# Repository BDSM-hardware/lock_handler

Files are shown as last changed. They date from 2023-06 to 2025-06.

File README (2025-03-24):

This module handles a collective bondage and/or multiple points self bondage.
It checks all the locks are closed and locks. If the lock is lost for one, all the locks unlock.

For the details, see the INSTALL file.

It has many LED to follow the procedure and see where is the problem, if so.
For each channel, a green and an amber LED tells if it is detected or not.
If all the detections of all the modules are on, the LEDs switch off and an amber LED per module illuminates.
When it is locked the amber switches off and a set of 2 red LED illuminates.
If a module is unused a switch turns everything off, tells to the daisy-chain it is OK, discards the lock command and illuminates a blue LED.

It is designed as small modules of 4 detection inputs. There is a daisy-chain in between.
* Mode 1: The system waits everybody is ready to lock, and illuminate an all ready LED. By connecting two wires to each other, it locks. By opening or shorting to the ground, it unlocks.
* Mode 2: It is similar to mode 1 but it locks as soon as everybody is ready without external action (remote control, timer etc...). This spares some wires.

Each input channel has a soft and a hard input. There is a dilemma between:
* a too strong detection that can detect the bondage is open, and unlock everybody.
* a too soft detection that can make a lock opening later.
To fix that, the hard and the soft are needed to lock. Only the soft is needed to maintain.
If a switch style detection is used, that can be done with 2 switches. If a metal detector style detection is used, it is two thresholds.
If this feature is not used, the two can be connected together.

It is a component.
* The output is a transistor. The user can add the power circuits needed against the lock chosen (electro magnet, pneumatic output etc...).
* The board is designed to run in stand alone mode with switches directly cconnected or with an additional board. It is mostly a metal detector style circuit. However, some components differs.

There is no circuit to program, no PIC, noFPGA, noCPLD etc... It works as soon as the 74HCxx and other components are soldered. It uses through hole components, not SMD.

Some VHDL files are provided to describe the behaviour in a more human-readable way.
A test is provided to check the truth table is the same for both the behaviour file and the file exported from the schematic.

TODO
* Add instructions using the bottom silk
* Build a prototype

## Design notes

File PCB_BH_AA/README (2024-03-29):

To get the files of the 2 inputs versions, switch to the lock_handler_2 branch.

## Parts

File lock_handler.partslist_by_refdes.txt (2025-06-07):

.START
..refdes	device	value	tolerance	comment	footprint	quantity
C1	CAPACITOR	4.7uF	20%	/	100mil	1
C11	POLARIZED_CAPACITOR	4.7uF	20%	Neg supply only	unknown	1
C12	POLARIZED_CAPACITOR	4.7uF	20%	Neg supply only	unknown	1
C13	POLARIZED_CAPACITOR	4.7uF	20%	Neg supply only	unknown	1
C14	POLARIZED_CAPACITOR	4.7uF	20%	Neg supply only	unknown	1
C15	CAPACITOR	2.2uF	20%	MLCC	2.54	1
C16	CAPACITOR	2.2uF	20%	MLCC	2.54	1
C17	CAPACITOR	2.2uF	20%	MLCC	2.54	1
C18	CAPACITOR	2.2uF	20%	MLCC	2.54	1
C19	CAPACITOR	2.2uF	20%	MLCC	2.54	1
C2	CAPACITOR	4.7uF	20%	/	100mil	1
C20	CAPACITOR	2.2uF	20%	MLCC	2.54	1
C21	CAPACITOR	2.2uF	20%	MLCC	2.54	1
C22	CAPACITOR	2.2uF	20%	MLCC	2.54	1
C23	POLARIZED_CAPACITOR	22uF	20%	tantale 50V	1000mil	1
C24	POLARIZED_CAPACITOR	220uF	40%	aluminium 16V	800mil	1
C25	POLARIZED_CAPACITOR	10uF	20%	or more	200mil	1
C26	POLARIZED_CAPACITOR	10uF	20%	or more	200mil	1
C27	CAPACITOR	1uF	20%	or more	100mil	1
C28	CAPACITOR	1uF	20%	or more	100mil	1
C29	CAPACITOR	1uF	20%	or more	100mil	1
C3	CAPACITOR	4.7uF	unknown	unknown	100mil	1
C30	CAPACITOR	1uF	20%	or more	100mil	1
C31	CAPACITOR	2.2uF	20%	MLCC	2.54	1
C4	CAPACITOR	4.7uF	unknown	unknown	100mil	1
C5	CAPACITOR	4.7uF	unknown	unknown	100mil	1
C6	CAPACITOR	4.7uF	20%	/	100mil	1
CONN_ABCD_DATA	CONNECTOR_7	/	/	/	SIP7N	1
CONN_ABCD_POWER	CONNECTOR_7	unknown	unknown	unknown	SIP7N	1
CONN_CHAIN	CONNECTOR_6	/	/	/	SIP6N	1
CONN_CHAIN_NEXT	CONNECTOR_6	/	/	/	SIP6N	1
CONN_DISABLE	CONNECTOR_2	/	/	/	SIP2N	1
CONN_NO_N_S	CONNECTOR_2	unknown	unknown	Neg supply to ground	SIP2N	1
CONN_OUTPUT	CONNECTOR_3	/	/	/	SIP3N	1
CONN_POWER	CONNECTOR_8	/	/	/	SIP8N	1
CONN_POWER_NEXT	CONNECTOR_8	/	/	/	SIP8N	1
CONN_RING	CONNECTOR_2	unknown	/	/	SIP2N	1
D10	DIODE	1N4148	/	Neg supply only	300mil	1
D11	DIODE	BA158	/	/	400mil	1
D12	DIODE	BA158	/	Neg supply only	400mil	1
D13	DIODE	BA158	/	/	400mil	1
D3	DIODE	1N4148	/	Neg supply only	300mil	1
D4	DIODE	1N4148	/	Neg supply only	300mil	1
D5	DIODE	1N4148	/	Neg supply only	300mil	1
D6	DIODE	1N4148	/	Neg supply only	300mil	1
D7	DIODE	1N4148	/	Neg supply only	300mil	1
D8	DIODE	1N4148	/	Neg supply only	300mil	1
D9	DIODE	1N4148	/	Neg supply only	300mil	1
LED1	LED	C503B-BCN	/	bleue	5.08	1
LED10	LED	C503B-ACN	/	amber	5.08	1
LED11	LED	C503B-RCN	/	red	5.08	1
LED12	LED	C503B-RCN	/	red	5.08	1
LED13	LED	C503B-WCN	/	white	5.08	1
LED2	LED	C503B-GCN	/	green	5.08	1
LED3	LED	C503B-ACN	/	amber	5.08	1
LED4	LED	C503B-GCN	/	green	5.08	1
LED5	LED	C503B-ACN	/	amber	5.08	1
LED6	LED	C503B-GCN	/	green	5.08	1
LED7	LED	C503B-ACN	/	amber	5.08	1
LED8	LED	C503B-GCN	/	green	5.08	1
LED9	LED	C503B-ACN	/	amber	5.08	1
Q1	NPN_TRANSISTOR	2N3904	Or equiv. CBE	/	TO92	1
Q2	NPN_TRANSISTOR	2N3904	Or equiv. CBE	/	TO92	1
Q3	darlington, NPN	TIP120	/	Or equiv. BCE darlington Vce twice the lock voltage	TO92	1
R14	RESISTOR	1.15K	10%, R211 to R217 diff 1%	/	500mil	1
R15	RESISTOR	1.15K	10%, R211 to R217 diff 1%	/	500mil	1
R16	RESISTOR	1.15K	10%, R211 to R217 diff 1%	/	500mil	1
R17	RESISTOR	1.15K	10%, R211 to R217 diff 1%	/	500mil	1
R18	RESISTOR	1.15K	10%, R211 to R217 diff 1%	/	500mil	1
R19	RESISTOR	1.15K	10%, R211 to R217 diff 1%	/	500mil	1
R20	RESISTOR	1.15K	10%, R211 to R217 diff 1%	/	500mil	1
R21	RESISTOR	1.15K	10%, R211 to R217 diff 1%	/	500mil	1
R22	RESISTOR	1.15K	10%, R211 to R217 diff 1%	/	500mil	1
R23	RESISTOR	1.15K	10%, R211 to R217 diff 1%	/	500mil	1
R24	RESISTOR	1.15K	10%, R211 to R217 diff 1%	/	500mil	1
R25	RESISTOR	1.15K	10%, R211 to R217 diff 1%	/	500mil	1
R26	RESISTOR	2.7K	10%	/	500mil	1
R27	RESISTOR	2.7K	10%	/	500mil	1
R28	RESISTOR	47.5	10%	/	500mil	1
R29	RESISTOR	22.1R	10%	/	500mil	1
R30	RESISTOR	4.7K	10%	/	500mil	1
R31	RESISTOR	4.7K	10%	/	500mil	1
R32	RESISTOR	348K	10%	/	500mil	1
R33	RESISTOR	10K	10%	/	500mil	1
R34	RESISTOR	10K	10%	/	500mil	1
R35	RESISTOR	10K	10%	/	500mil	1
R36	RESISTOR	10K	10%	/	500mil	1
R37	RESISTOR	22.1R	10%	/	500mil	1
R38	RESISTOR	22.1R	10%	/	500mil	1
R39	RESISTOR	4.7K	10%	/	500mil	1
R40	RESISTOR	22.1R	10%	/	500mil	1
R41	RESISTOR	10K	10%	/	500mil	1
R42	RESISTOR	22.1R	10%	/	500mil	1
R43	RESISTOR	1K	10%	value half the lock device resistance	500mil	1
R44	RESISTOR	1.15K	10%	/	500mil	1
R45	RESISTOR	221K	10%	/	500mil	1
R46	RESISTOR	4.75K	10%	/	500mil	1
R47	RESISTOR	4.75K	10%	/	500mil	1
R48	RESISTOR	221K	10%	/	500mil	1
R49	RESISTOR	4.75K	10%	/	500mil	1
R50	RESISTOR	4.75K	10%	/	500mil	1
R51	RESISTOR	221K	10%	/	500mil	1
R52	RESISTOR	4.75K	10%	/	500mil	1
R53	RESISTOR	4.75K	10%	/	500mil	1
R54	RESISTOR	221K	10%	/	500mil	1
R55	RESISTOR	4.75K	10%	/	500mil	1
R56	RESISTOR	4.75K	10%	/	500mil	1
R57	RESISTOR	221K	10%	/	500mil	1
R58	RESISTOR	4.75K	10%	/	500mil	1
R59	RESISTOR	4.75K	10%	/	500mil	1
R60	RESISTOR	221K	10%	/	500mil	1
R61	RESISTOR	4.75K	10%	/	500mil	1
R62	RESISTOR	4.75K	10%	/	500mil	1
R63	RESISTOR	221K	10%	/	500mil	1
R64	RESISTOR	4.75K	10%	/	500mil	1
R65	RESISTOR	4.75K	10%	/	500mil	1
R66	RESISTOR	221K	10%	/	500mil	1
R67	RESISTOR	4.75K	10%	/	500mil	1
R68	RESISTOR	4.75K	10%	/	500mil	1
R69	RESISTOR	681R	2%	/	500mil	1
R70	RESISTOR	681R	2%	or zener diode	500mil	1
R71	RESISTOR	681R	2%	or zener diode	500mil	1
R76	RESISTOR	2.21K	2%	Switches only	500mil	1
R77	RESISTOR	2.21K	2%	Switches only	500mil	1
R78	RESISTOR	2.21K	2%	Switches only	500mil	1
R79	RESISTOR	2.21K	2%	Switches only	500mil	1
R80	RESISTOR	4.7K	10%	/	500mil	1
R81	RESISTOR	22.1R	10%	/	500mil	1
RP45	RESISTORPACK_9	10K	10%	Neg supply only	8X100mil	1
U1	7400	74HC00	/	/	DIP14	1
U10	7404	74HC04	/	/	DIP14	1
U11	QUAD_OPAMP	TLV9144IN	/	/	DIL14	1
U12	QUAD_OPAMP	TLV9144IN	/	/	DIL14	1
U13	icl7660	unknown	/	Neg supply only	DIL8	1
U14	7806	7806	/	7805 or 7806	TO220	1
U15	7906	7906	unknown	Neg supply only	TO220	1
U16	7809	unknown	unknown	Neg supply and alim > 10V	TO220	1
U2	7402	74HC02	/	/	DIP14	1
U3	7404	74HC04	/	/	DIP14	1
U4	7420	74HC20	/	/	DIP14	1
U5	7400	74HC00	/	/	DIP14	1
U7	7400	74HC00	/	/	DIP14	1
U8	7400	74HC00	/	/	DIP14	1
U9	74132	74HC132	/	/	DIP14	1
.END

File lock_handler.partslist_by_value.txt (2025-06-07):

.START
..device	value	tolerance	comment	footprint	quantity	refdes
7400	74HC00	/	/	DIP14	4	U1 U5 U7 U8
7402	74HC02	/	/	DIP14	1	U2
7404	74HC04	/	/	DIP14	2	U10 U3
74132	74HC132	/	/	DIP14	1	U9
7420	74HC20	/	/	DIP14	1	U4
7806	7806	/	7805 or 7806	TO220	1	U14
7809	unknown	unknown	Neg supply and alim > 10V	TO220	1	U16
7906	7906	unknown	Neg supply only	TO220	1	U15
CAPACITOR	1uF	20%	or more	100mil	4	C27 C28 C29 C30
CAPACITOR	2.2uF	20%	MLCC	2.54	9	C15 C16 C17 C18 C19 C20 C21 C22 C31
CAPACITOR	4.7uF	20%	/	100mil	3	C1 C2 C6
CAPACITOR	4.7uF	unknown	unknown	100mil	3	C3 C4 C5
CONNECTOR_2	/	/	/	SIP2N	1	CONN_DISABLE
CONNECTOR_2	unknown	/	/	SIP2N	1	CONN_RING
CONNECTOR_2	unknown	unknown	Neg supply to ground	SIP2N	1	CONN_NO_N_S
CONNECTOR_3	/	/	/	SIP3N	1	CONN_OUTPUT
CONNECTOR_6	/	/	/	SIP6N	2	CONN_CHAIN CONN_CHAIN_NEXT
CONNECTOR_7	/	/	/	SIP7N	1	CONN_ABCD_DATA
CONNECTOR_7	unknown	unknown	unknown	SIP7N	1	CONN_ABCD_POWER
CONNECTOR_8	/	/	/	SIP8N	2	CONN_POWER CONN_POWER_NEXT
darlington, NPN	TIP120	/	Or equiv. BCE darlington Vce twice the lock voltage	TO92	1	Q3
DIODE	1N4148	/	Neg supply only	300mil	8	D10 D3 D4 D5 D6 D7 D8 D9
DIODE	BA158	/	/	400mil	2	D11 D13
DIODE	BA158	/	Neg supply only	400mil	1	D12
icl7660	unknown	/	Neg supply only	DIL8	1	U13
LED	C503B-ACN	/	amber	5.08	5	LED10 LED3 LED5 LED7 LED9
LED	C503B-BCN	/	bleue	5.08	1	LED1
LED	C503B-GCN	/	green	5.08	4	LED2 LED4 LED6 LED8
LED	C503B-RCN	/	red	5.08	2	LED11 LED12
LED	C503B-WCN	/	white	5.08	1	LED13
NPN_TRANSISTOR	2N3904	Or equiv. CBE	/	TO92	2	Q1 Q2
POLARIZED_CAPACITOR	10uF	20%	or more	200mil	2	C25 C26
POLARIZED_CAPACITOR	220uF	40%	aluminium 16V	800mil	1	C24
POLARIZED_CAPACITOR	22uF	20%	tantale 50V	1000mil	1	C23
POLARIZED_CAPACITOR	4.7uF	20%	Neg supply only	unknown	4	C11 C12 C13 C14
QUAD_OPAMP	TLV9144IN	/	/	DIL14	2	U11 U12
RESISTOR	1.15K	10%	/	500mil	1	R44
RESISTOR	1.15K	10%, R211 to R217 diff 1%	/	500mil	12	R14 R15 R16 R17 R18 R19 R20 R21 R22 R23 R24 R25
RESISTOR	10K	10%	/	500mil	5	R33 R34 R35 R36 R41
RESISTOR	1K	10%	value half the lock device resistance	500mil	1	R43
RESISTOR	2.21K	2%	Switches only	500mil	4	R76 R77 R78 R79
RESISTOR	2.7K	10%	/	500mil	2	R26 R27
RESISTOR	22.1R	10%	/	500mil	6	R29 R37 R38 R40 R42 R81
RESISTOR	221K	10%	/	500mil	8	R45 R48 R51 R54 R57 R60 R63 R66
RESISTOR	348K	10%	/	500mil	1	R32
RESISTOR	4.75K	10%	/	500mil	16	R46 R47 R49 R50 R52 R53 R55 R56 R58 R59 R61 R62 R64 R65 R67 R68
RESISTOR	4.7K	10%	/	500mil	4	R30 R31 R39 R80
RESISTOR	47.5	10%	/	500mil	1	R28
RESISTOR	681R	2%	/	500mil	1	R69
RESISTOR	681R	2%	or zener diode	500mil	2	R70 R71
RESISTORPACK_9	10K	10%	Neg supply only	8X100mil	1	RP45
.END

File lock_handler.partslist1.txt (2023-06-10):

.START
..refdes	device	value	tolerance	comment	footprint	quantity
C200	CAPACITOR	2.2uF	20%	/	2.54	1
C201	CAPACITOR	2.2uF	20%	/	2.54	1
C202	CAPACITOR	2.2uF	20%	/	2.54	1
C203	CAPACITOR	2.2uF	20%	MLCC	2.54	1
C204	CAPACITOR	2.2uF	20%	MLCC	2.54	1
C205	CAPACITOR	2.2uF	20%	MLCC	2.54	1
C206	CAPACITOR	2.2uF	20%	MLCC	2.54	1
C207	CAPACITOR	2.2uF	20%	MLCC	2.54	1
C208	CAPACITOR	2.2uF	20%	MLCC	2.54	1
C209	CAPACITOR	2.2uF or 1nF	10%	/	2.54	1
C210	CAPACITOR	2.2uF or 1nF	10%	/	2.54	1
C211	CAPACITOR	2.2uF or 1nF	10%	/	2.54	1
C212	CAPACITOR	2.2uF or 1nF	10%	/	2.54	1
C213	POLARIZED_CAPACITOR	22uF	20%	tantale 50V	5.08	1
C214	POLARIZED_CAPACITOR	220uF	40%	aluminium 16V	2000mil	1
CONN_AB_HARDSOFT	CONNECTOR_7	/	/	/	SIP7N	1
CONN_AB_POWER	CONNECTOR_7	/	/	Elec detec. only	SIP7N	1
CONN_CHAIN	CONNECTOR_6	/	/	/	SIP6N	1
CONN_CHAIN_NEXT	CONNECTOR_6	/	/	/	SIP6N	1
CONN_DISABLE	CONNECTOR_2	/	/	/	SIP2N	1
CONN_OUTPUT	CONNECTOR_3	/	/	/	SIP3N	1
CONN_POWER	CONNECTOR_8	/	/	/	SIP8N	1
CONN_POWER_NEXT	CONNECTOR_8	/	/	/	SIP8N	1
CONN_RING	CONNECTOR_2	/	/	/	SIP2N	1
D200	DIODE	BA158	/	/	300mil	1
D201	DIODE	1N4148	/	Elec detec. only	300mil	1
D202	DIODE	1N4148	/	Elec detec. only	300mil	1
D203	DIODE	1N4148	/	Elec detec. only	300mil	1
D204	DIODE	1N4148	/	Elec detec. only	300mil	1
D205	DIODE	BA158	/	/	300mil	1
LED1	LED	C503B-BCN	/	bleue	5.08	1
LED2	LED	C503B-GCN	/	green	5.08	1
LED3	LED	C503B-ACN	/	amber	5.08	1
LED4	LED	C503B-GCN	/	green	5.08	1
LED5	LED	C503B-ACN	/	amber	5.08	1
LED6	LED	C503B-ACN	/	amber	5.08	1
LED7	LED	C503B-RCN	/	red	5.08	1
LED8	LED	C503B-RCN	/	red	5.08	1
Q200	NPN_TRANSISTOR	2N3904	Or equiv. CBE	/	TO92	1
Q201	darlington, NPN	TIP120	/	Or equiv. BCE darlington Vce twice the lock voltage	TO92	1
Q202	7806	7806	/	7805 or 7806	TO220	1
R200	RESISTOR	4.7K	10%	/	500mil	1
R201	RESISTOR	348K	10%	/	500mil	1
R202	RESISTOR	4.7K	10%	/	500mil	1
R203	RESISTOR	47.5	10%	/	500mil	1
R204	RESISTOR	10K	10%	/	500mil	1
R205	RESISTOR	10K	10%	/	500mil	1
R206	RESISTOR	22.1	10%	/	500mil	1
R207	RESISTOR	22.1	10%	/	500mil	1
R208	RESISTOR	22.1	10%	/	500mil	1
R209	RESISTOR	22.1	10%	/	500mil	1
R210	RESISTOR	10K	10%	/	500mil	1
R211	RESISTOR	1.15K	10%, R211 to R217 diff 1%	/	500mil	1
R212	RESISTOR	1.15K	10%, R211 to R217 diff 1%	/	500mil	1
R213	RESISTOR	1.15K	10%, R211 to R217 diff 1%	/	500mil	1
R214	RESISTOR	1.15K	10%, R211 to R217 diff 1%	/	500mil	1
R215	RESISTOR	1.15K	10%, R211 to R217 diff 1%	/	500mil	1
R216	RESISTOR	1.15K	10%, R211 to R217 diff 1%	/	500mil	1
R217	RESISTOR	1.15K	10%, R211 to R217 diff 1%	/	500mil	1
R218	RESISTOR	1.15K	10%	/	500mil	1
R219	RESISTOR	1K	10%	value half the lock device resistance	500mil	1
R220	RESISTOR	22.1	10%	Switch detec. only	500mil	1
R221	RESISTOR	22.1	10%	Switch detec. only	500mil	1
R222	RESISTOR	22.1	10%	Switch detec. only	500mil	1
R223	RESISTOR	22.1	10%	Switch detec. only	500mil	1
R224	RESISTOR	22.1	10%	/	500mil	1
R225	RESISTOR	22.1	10%	/	500mil	1
R226	RESISTOR	22.1	10%	/	500mil	1
R227	RESISTOR	22.1	10%	/	500mil	1
R228	RESISTORPACK_5	4.7K	10%, diff. 10%	Elec detec. only	2.54	1
R229	RESISTORPACK_5	4.7K	10%, diff. 10%	NC Switch detec. only	2.54	1
R230	RESISTORPACK_5	10K	10%, diff. 10%	NO Switch detec. only	2.54	1
R231	RESISTOR	22.1	10%	NO Switch detec. only	500mil	1
R232	RESISTOR	22.1	10%	NO Switch detec. only	500mil	1
R233	RESISTOR	10K	10%	/	500mil	1
U200	74132	74HC132	/	/	DIP14	1
U201	7404	74HC04	/	/	DIP14	1
U202	7402	74HC02	/	/	DIP14	1
U203	7402	74HC02	/	/	DIP14	1
U204	7410	74HC10	/	/	DIP14	1
U205	7404	74HC04	/	/	DIP14	1
.END

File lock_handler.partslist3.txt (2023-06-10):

.START
..device	value	tolerance	comment	footprint	quantity	refdes
7402	74HC02	/	/	DIP14	2	U202 U203
7404	74HC04	/	/	DIP14	2	U201 U205
7410	74HC10	/	/	DIP14	1	U204
74132	74HC132	/	/	DIP14	1	U200
7806	7806	/	7805 or 7806	TO220	1	Q202
CAPACITOR	2.2uF	20%	/	2.54	3	C200 C201 C202
CAPACITOR	2.2uF	20%	MLCC	2.54	6	C203 C204 C205 C206 C207 C208
CAPACITOR	2.2uF or 1nF	10%	/	2.54	4	C209 C210 C211 C212
CONNECTOR_2	/	/	/	SIP2N	2	CONN_DISABLE CONN_RING
CONNECTOR_3	/	/	/	SIP3N	1	CONN_OUTPUT
CONNECTOR_6	/	/	/	SIP6N	2	CONN_CHAIN CONN_CHAIN_NEXT
CONNECTOR_7	/	/	/	SIP7N	1	CONN_AB_HARDSOFT
CONNECTOR_7	/	/	Elec detec. only	SIP7N	1	CONN_AB_POWER
CONNECTOR_8	/	/	/	SIP8N	2	CONN_POWER CONN_POWER_NEXT
darlington, NPN	TIP120	/	Or equiv. BCE darlington Vce twice the lock voltage	TO92	1	Q201
DIODE	1N4148	/	Elec detec. only	300mil	4	D201 D202 D203 D204
DIODE	BA158	/	/	300mil	2	D200 D205
LED	C503B-ACN	/	amber	5.08	3	LED3 LED5 LED6
LED	C503B-BCN	/	bleue	5.08	1	LED1
LED	C503B-GCN	/	green	5.08	2	LED2 LED4
LED	C503B-RCN	/	red	5.08	2	LED7 LED8
NPN_TRANSISTOR	2N3904	Or equiv. CBE	/	TO92	1	Q200
POLARIZED_CAPACITOR	220uF	40%	aluminium 16V	2000mil	1	C214
POLARIZED_CAPACITOR	22uF	20%	tantale 50V	5.08	1	C213
RESISTOR	1.15K	10%	/	500mil	1	R218
RESISTOR	1.15K	10%, R211 to R217 diff 1%	/	500mil	7	R211 R212 R213 R214 R215 R216 R217
RESISTOR	10K	10%	/	500mil	4	R204 R205 R210 R233
RESISTOR	1K	10%	value half the lock device resistance	500mil	1	R219
RESISTOR	22.1	10%	/	500mil	12	R206 R207 R208 R209 R220 R221 R222 R223 R224 R225 R226 R227
RESISTOR	22.1	10%	NO Switch detec. only	500mil	2	R231 R232
RESISTOR	348K	10%	/	500mil	1	R201
RESISTOR	4.7K	10%	/	500mil	2	R200 R202
RESISTOR	47.5	10%	/	500mil	1	R203
RESISTORPACK_5	10K	10%, diff. 10%	NO Switch detec. only	2.54	1	R230
RESISTORPACK_5	4.7K	10%, diff. 10%	Elec detec. only	2.54	1	R228
RESISTORPACK_5	4.7K	10%, diff. 10%	NC Switch detec. only	2.54	1	R229
.END

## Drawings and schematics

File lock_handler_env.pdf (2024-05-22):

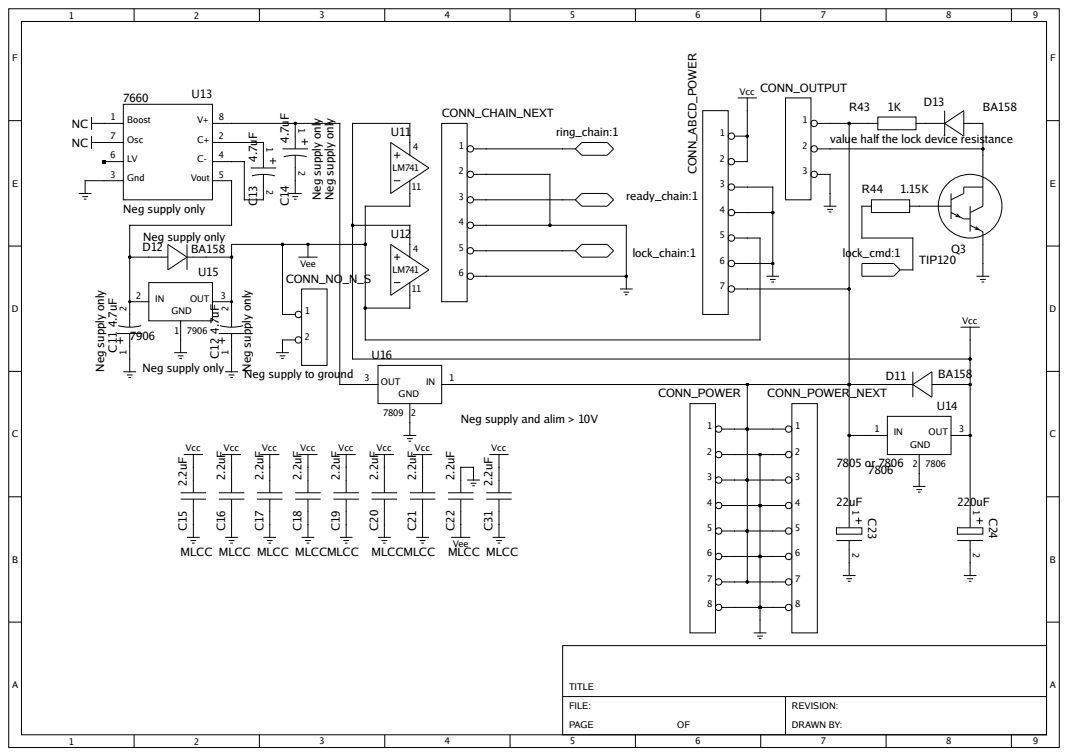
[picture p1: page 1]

value half the lock device resistance

Neg supply to ground

Neg supply and alim > 10V

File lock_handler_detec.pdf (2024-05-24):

TL064 56

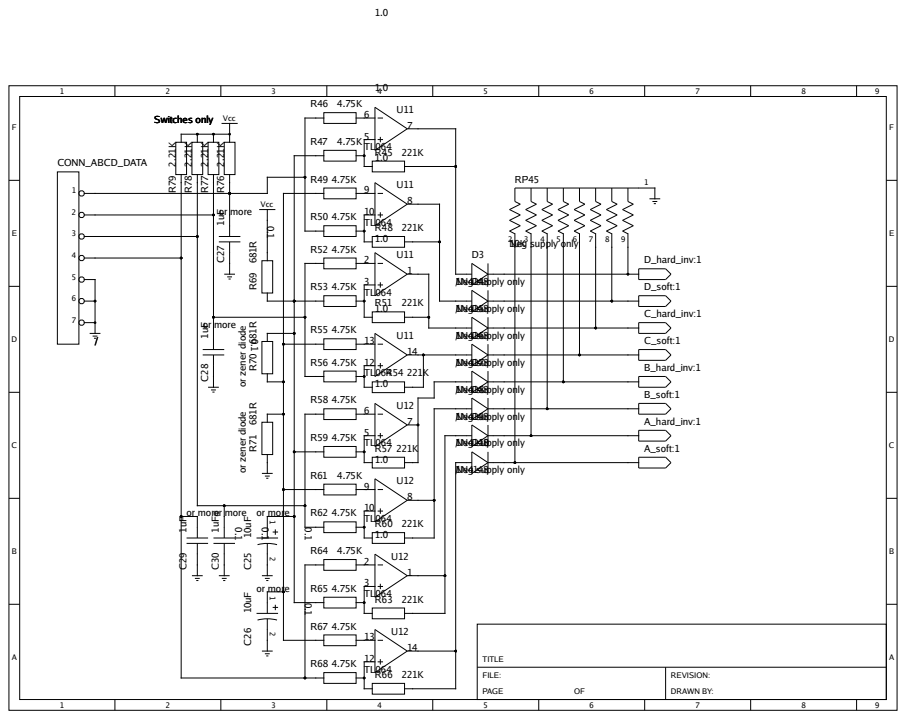
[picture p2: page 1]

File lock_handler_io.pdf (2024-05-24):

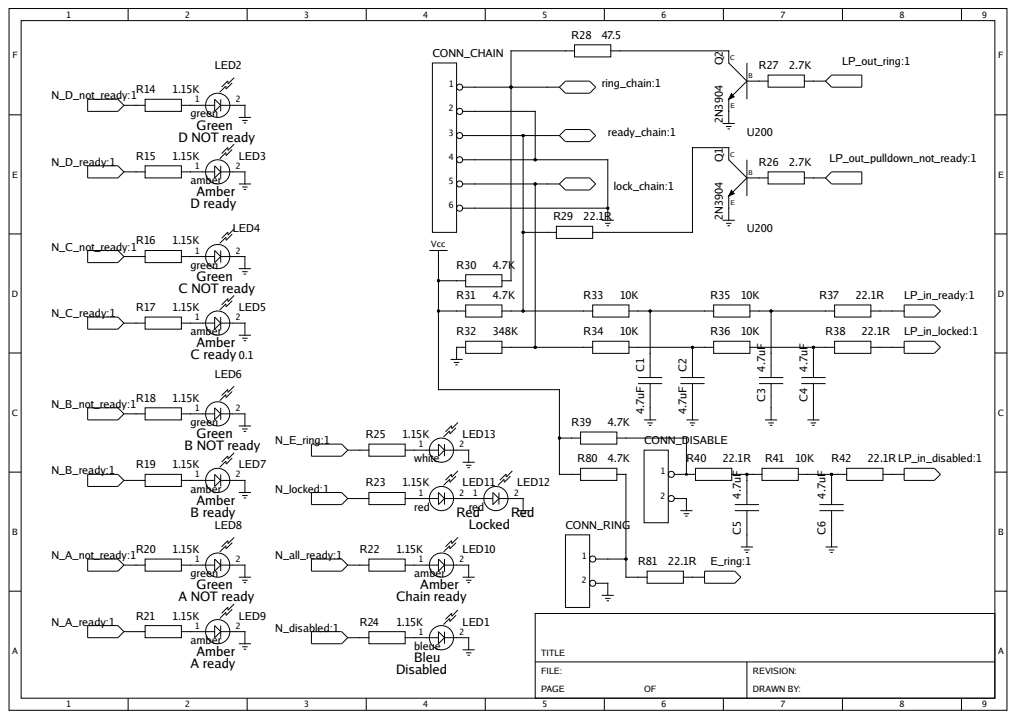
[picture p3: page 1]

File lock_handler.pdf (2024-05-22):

74HC04 1

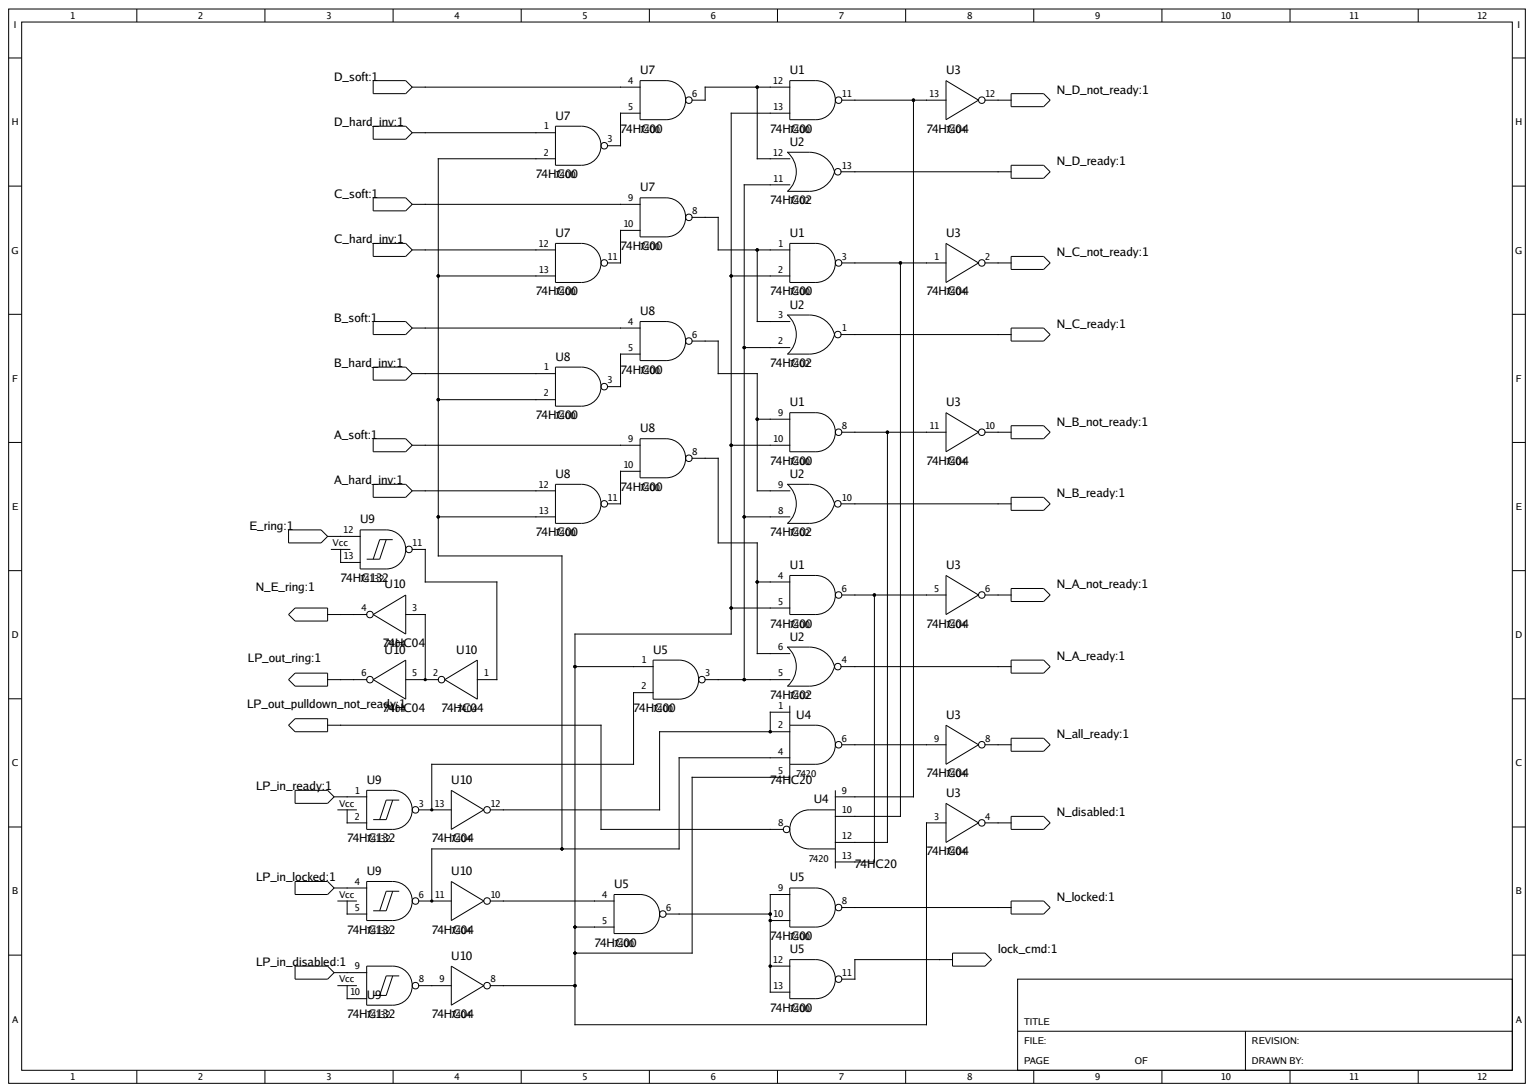
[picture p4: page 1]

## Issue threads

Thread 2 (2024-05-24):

Ring button input forgotten

BDSM-hardware, 2024-05-24:
In the 4 locks version, the ring button has been integrated into the design.
Unfortunately their inputs has been forgotten.

BDSM-hardware, 2024-05-24:
Work around if one does not use the ring button:
strap the pins 12 and 13 of U9 together.
Work around if one uses the ring button and has already made the PCB:
add R80 and R81 with some silicone and wires. It is not that difficult, see the new versions of the PCB

BDSM-hardware, 2024-05-24:
Fixed

Closed 2024-05-24.

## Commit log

2023-05-09 Initial files
    [lock_handler.sch]
2023-05-14 Improve the naming of the files.
    lock_handler.eps beomes lock_handler.pcb.ps
    more ps files are comming with pcb details or schematics export
2023-05-14 Some improvements
    * More .ps and/or .pdf exports
    * Partlists exports
    * PCB went forward
    [lock_handler.sch]
2023-05-14 More PCB work
    * Add room for the decoupling capacitors
    * Draw power supplies, and add high speed printed decoupling capacitors
    * Add mounting screw and partial outline
    * Add a plane for the LED cut out
2023-05-15 More PCB and fix a PS export problem
2023-05-26 More work
    Add a schematic for the decoupling and the passive components for the standalone mode (simple switches)
    The lock_handler.sch schematic is in RC state.
    PCB: Daisy chain passive components completed.
    PCB: Estimation of the passive components of the switches.
    PCB: complete Vcc and ground planes, including some high frequency printed low value decoupling.
    The top of the PCB is in RC state.
    [lock_handler.sch, lock_handler_env.sch]
2023-05-26 Fix a lock_handler.pcb.ps not recognized on some systems
2023-05-28 More work
    * schematic: completed the input part
    * schematic: added the voltage regulator
    * partslists exports: added the columns toleance and comment
    * pcb: improved
    [lock_handler.sch, lock_handler_env.sch]
2023-06-02 Schematic and PCB work
    All the schematics diagrams are now in RC state
    Dimensions of the PCB are now known
    Four components and 34 rat lines are remaining
    [lock_handler.sch, lock_handler_env.sch]
2023-06-02 Fix a clip problem for the .ps export of the PCB
2023-06-10 All schematic and partslist files in RC state
    Before release
    * PCB file is going to be committed
    * Some verification is needed
    * An export in Gerbert is going to be done
    [lock_handler.sch, lock_handler_env.sch]
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2023-06-11 RC of the project
    RC state of the pcb file
    Initial release of the Gerber exports
    [PCB_BH_AA.bottom.gbr, PCB_BH_AA.bottommask.gbr, PCB_BH_AA.bottompaste.gbr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]
2023-12-17 Mechanical drawings updates
    Precise quotation added.
    Corners for the 1591D box.
    TODO: improve the box drawings.
    [PCB_BH_AA.bottom.gbr, PCB_BH_AA.bottommask.gbr, PCB_BH_AA.bottompaste.gbr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]
2024-01-04 Fix a resistor too high
    [lock_handler.sch]
2024-01-04 Initial version of the 4 channels
    [lock_handler.sch, lock_handler_io.sch]
2024-01-07 Some progress
    * Schematics of the logic part close to the RC
    * VHDL exports of the logic part. TODO update the test as well.
    * Some PCB
    4 Channels make the things easy as the logic circuits are organised as 4 gates per component.
    [lock_handler.sch]
2024-01-12 Numerical part close the the RC
    Many copy-paste or move to 4 channels bugs
    Some files might not yet been updated
    * Bug fixes in the behavior
    * Bug fixes in the schematic, around U7 and U8, the schematic wasn't updated
    * Update the test vhdl software
    * Now the test runs successfully
    TODO
    some soft and hard detection input interfaces
    [lock_handler.sch, lock_handler_env.sch, lock_handler_io.sch]
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2024-01-19 More PCB and input interface
    This new version includes the input comparators with hysteresis.
    Regardless the detection methods, it is always a soft and a hard threshold.
    Soft and hard comparators are going to be wired while toggling their inputs. By this way, the inverter 74HC04 circuit goes out.
    [lock_handler.sch, lock_handler_env.sch, lock_handler_io.sch]
2024-02-08 Some PCB and schematics
    The operational amplifiers has now their positive feedback resistors to get a comparator.
    ... and it is drawn.
    [lock_handler_detec.sch, lock_handler_env.sch, lock_handler_io.sch]
2024-02-11 More PCB more schematic
    The schematic is now close to be complete
    [lock_handler_detec.sch]
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2024-03-05 More schematic and PCB work
    [lock_handler_detec.sch, lock_handler_env.sch]
2024-03-17 More PCB and box drawing
    [lock_handler_detec.sch, lock_handler_env.sch]
2024-03-23 More schematic and PCB
    [lock_handler_env.sch]
2024-03-23 Removed the files of the lock_handler_2 branch from this lock_handler_4 branch
    [PCB_BH_AA.bottom.gbr, PCB_BH_AA.bottommask.gbr, PCB_BH_AA.bottompaste.gbr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]
2024-04-16 PCB almost finished and documentation.
    [lock_handler_detec.sch, lock_handler_env.sch]
2024-05-04 RC PCB and Gerbert files
    [PCB_BH_AB.bottom.gbr, PCB_BH_AB.bottommask.gbr, PCB_BH_AB.bottompaste.gbr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]
2024-05-22 Partslists BUG + some cleanups
    Some missing data in the schema that displayed "unknown" in the partslist by value has been fixed
    My CAD software was buggy. Identical (compo.,value,tolerance) lines with different comments were merged while getting the comment of the first one.
    Some irrelevant tolerances was visible in the schematics.
    [lock_handler.sch, lock_handler_detec.sch, lock_handler_env.sch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]
2024-05-24 Fix the forgotten button issue + minor fixes has
    The ring button input has been added, R80 and R81 has been added as well
    The PCB has been updated. Unfortunately, there is no available room without a major redesign. R80 and R81 overlaps a little, but their pins too close are connected together.
    The README for the re-usage of the PCB as an operator board has been added.
    Some minor fixes, mostly on the silk, has been done.
    [PCB_BH_AB.bottom.gbr, PCB_BH_AB.bottommask.gbr, PCB_BH_AB.bottompaste.gbr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]
2024-05-24 Add more ground planes
    [PCB_BH_AB.bottom.gbr, PCB_BH_AB.bottommask.gbr, PCB_BH_AB.bottompaste.gbr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]
2024-06-09 Old file removal, box_meca updated
    The old file lock_handler.pcb.ps was renamed to lock_handler.topview.ps for a while.
    The mark of the leds was forgotten on the box meca plane.
    Irrelevant data has been cleanup on the box meca.
    No other change has been made.
    [PCB_BH_AB.box_meca.gbr]
2024-06-09 Old file removal, box_meca updated
    Irrelevant data has been cleaned up on the box meca.
    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
    [PCB_BH_AB.box_meca.gbr]
2025-06-07 TL064 changed into TLV9144IN
    TLV9144IN is now the official component.
    It has a very low consumption AND a large supply voltage scale.
    That fits for all the configurations 5V or 6V, with or without negative supply
    However everybody can use many other circuits after the configuration is chosen.
    [lock_handler_detec.sch]
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
